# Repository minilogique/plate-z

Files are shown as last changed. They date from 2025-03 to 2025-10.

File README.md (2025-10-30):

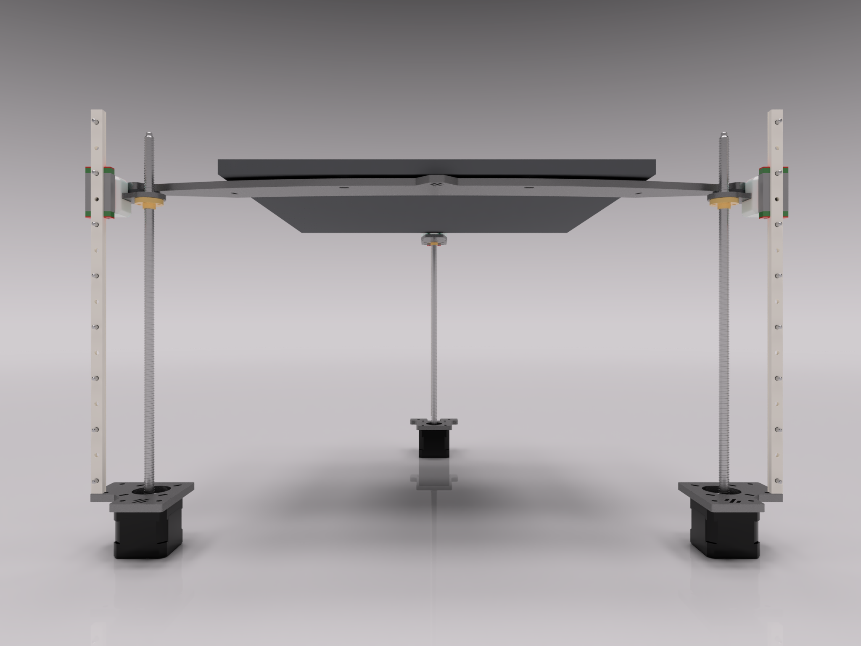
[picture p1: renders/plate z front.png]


A more industrial look and feel for the Voron Trident Z-assembly. Also greatly slims the whole Z-assembly and adds extra usable Z-height by making the bed itself as a part of the Z-kinematics. Keep in mind, that I do not own an official Voron but instead an adaption from Flying Bear Reborn 2 and this whole process is not complete and that the front carriers and carrier plates can be used to replace printed pieces as far as I'm concnerned, will check it once, again, I have gotten the CAD file of Trident. Flying Bear Reborn 2 owners are good to use these parts as in my printer it's been all happy for the last 200+ printing hours with more than 60C enclosure temperatures.

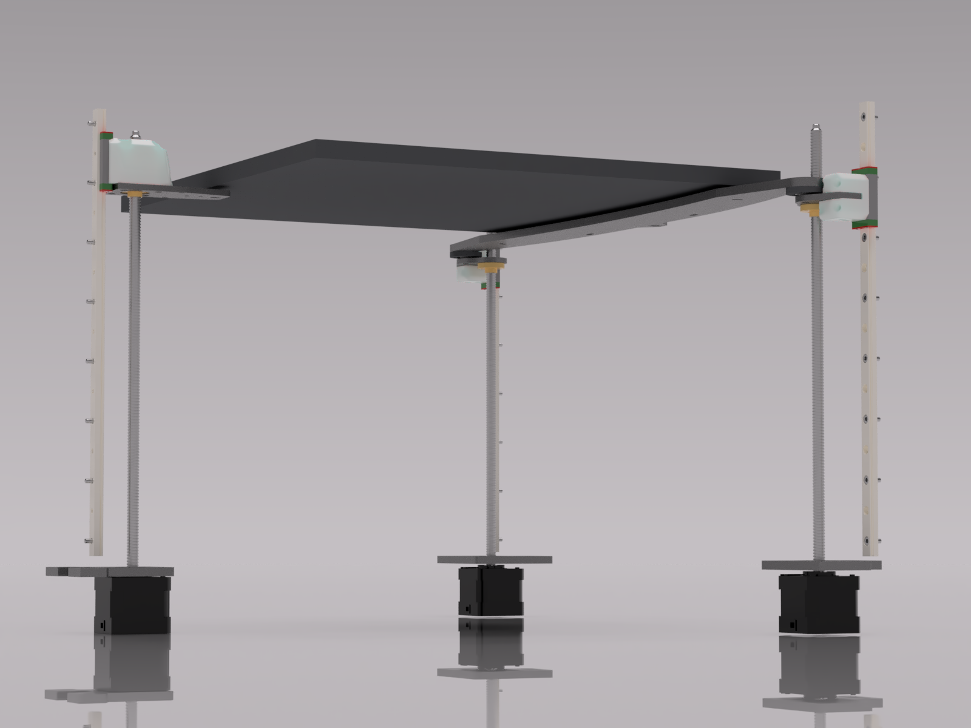
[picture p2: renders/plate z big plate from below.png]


The bigplate as I like to call it, is only piece connecting two points of the Z-gantry other than the bed itself. This is because of needed movements in case metal swells a bit bigger with heat and give way for the stress to go somewhere. I have yet to create the correct size bigplate for the bed because I created all this from a Trident 250 CAD and butchered it pretty badly. Flying Bear Reborn 2 owners are good to go as it's proven for hundres of hours and I have had no issues with it. Voron Trident bigplate DXFs will be created in near future after I have found the CAD files and correct measurements for Trident 250, 300 and 350.

I recommend to cut the front plates out of AT LEAST 4mm aluminium but go for 6mm, however I used 4mm stainless steel for fronts and 6mm for rear and everything is great. Seems that the rear stepper piece is happy with just two M4 bolts holding it in and it does not move nor bend under a bit more than normal printing conditions. Front plates have adjustabilty option to fine tune the stepper location as the bed will go really low compared to 2020 frame and otherwise very bulky assembly. The printable pieces that carry the plates are recommended to print from material that can resist at least 100C, be it ASA-CF or something better as the heat is conducted throughout the framing and noone wants plastic melt at wrong places.

The bigplate or big X-plate has to be cut from 6mm stainless steel. I might fear the aluminum might be a bit too bendy, but if your printer has 6mm bed it should be fine.

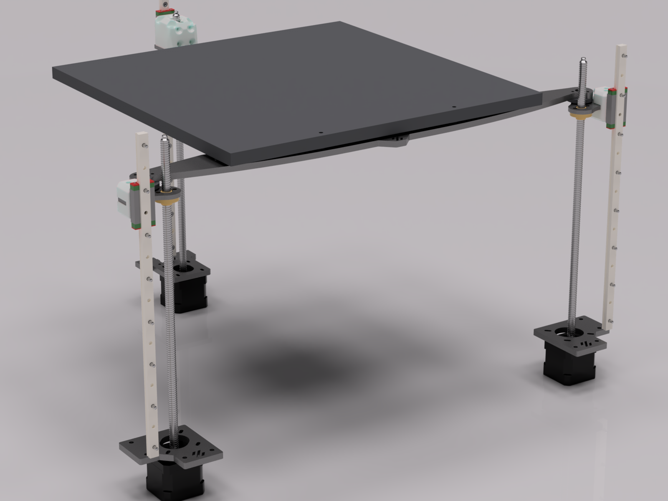
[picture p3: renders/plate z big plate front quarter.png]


To do this mod you might need to be able to quite possibly drill and tap your bed block for additional hardware.

Hardware I used with adapted Flying Bear Reborn 2 with Annex 350x350x12mm bed and 350mm version of FYSETCH 1000W heater:
- 8x M5x35 with nuts, washers are recommended; for attaching rear and front carriers to the plates. DO NOT overtighten the rear carrier as it might deform the part and misalign the rail cart bolt bores
- 4x M3x40 to attach rear plate carrier to the rear linear rail cart
- 10x M4x8 for 4mm stepper plates or 10x M4x10 for 6mm stepper plates
- 6x M3x12 with nuts for securing the spherical bearings from Voron BOM for front carriers, also these sandwich the bearings in place
- 6x M3x25 and 2x M3x20 for to attach printed front plate carriers to linear rail carts
- 2x M5x16 with nuts to tie X-plate and the spherical bearing together
- 6x M3x10 with nuts to attach brass Z-screws to front Z-assemblies or 6x M4x8 if you tap the threads into brass Z-screws and screw the bolts in them directly. Two bolts are enough, tighten them just enough that they are not loose and check after a while
- 2x M4x20 bolts if you dare to drill and tap two holes into the bed to secure the bigplate to it. Drill the holes in the middle of the ovals so it can still move, place an M5 nut for each of M4 bolts between the bigplate and bed to keep some space between the heater and bigplate so it is not siphoning too much heat from it
OR
2x M4x10 bolts if you just want to add two bolts in the plate as spacers to keep the heater away from the bigplate. I have it like this and the weight holds it steady.
- 2x M3x16 bolts close to the front corners of the bed. Again, holes have to be in the middle of the ovals to let the metals move. Most perfect solution would be with M3x20 bolts and with some really strong springs or couple of millimeters worth of springwashers.
- 12x M3x8, M3x10 or M3x12 bolts for steppers depending of what thickness you chose for the stepper plates - 4mm, 6mm or 8mm. You can add M3 slim washers to the top below the bolt heads. Screw them almost tight, back up half a turn, home the printer and then lower the bed as low as you can and adjust the steppers so the Z-screws are properly upright. Hold the Z-screws from the top and tighten one or two bolts per stepper and that is enough so you can raise the bed high enough for you to acces rest of the stepper bolts and tighten them properly
- 1x M3x16 bolt with a nut to the rear. Put the bolt in from the top of the bed, under the magnet line and tighten it. Once the bed is installed, add a spring or springwasher from below with another nut to secure it to the rear plate. Not the most elegant solution, but it's not designed be rigid and also not designed to be slanted more than few degrees. Bed will be held in position by front carriers and rear is just for support from a third point.

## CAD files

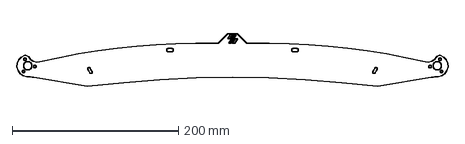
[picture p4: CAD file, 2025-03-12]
DXF/FBR2 bigplate X-plate.dxf
519.1 x 63.6 mm

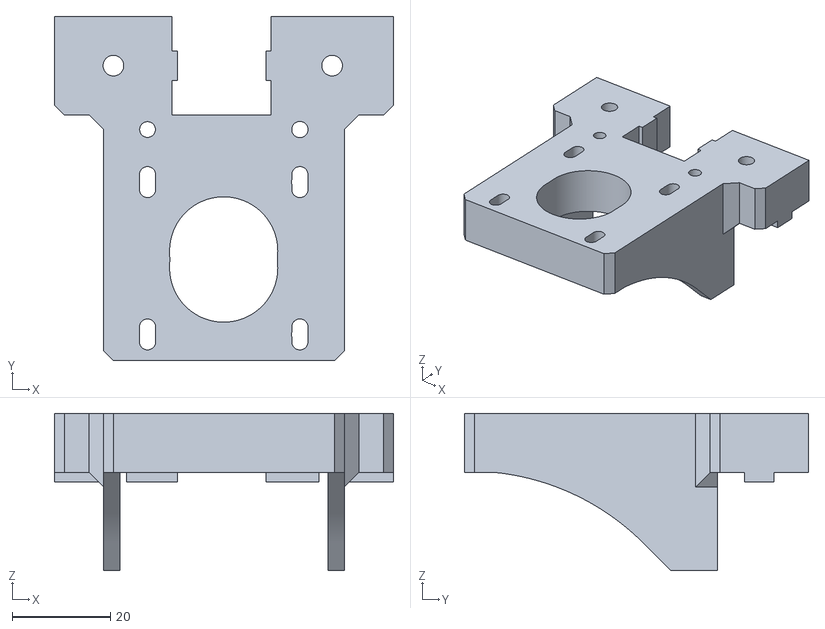
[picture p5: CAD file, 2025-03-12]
print files/plate-z printable rear stepper carrier.stl
69.0 x 70.0 x 32.0

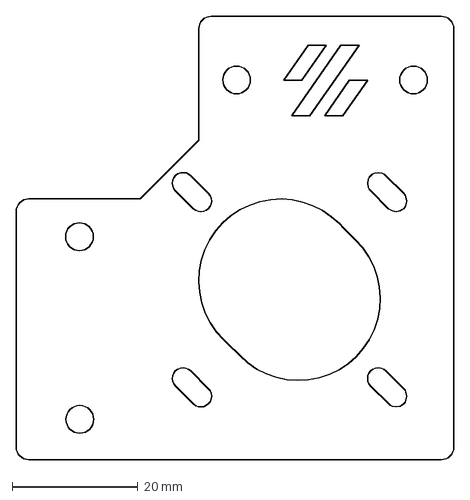
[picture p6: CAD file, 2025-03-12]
DXF/front right stepper plate.dxf
69.5 x 70.4 mm

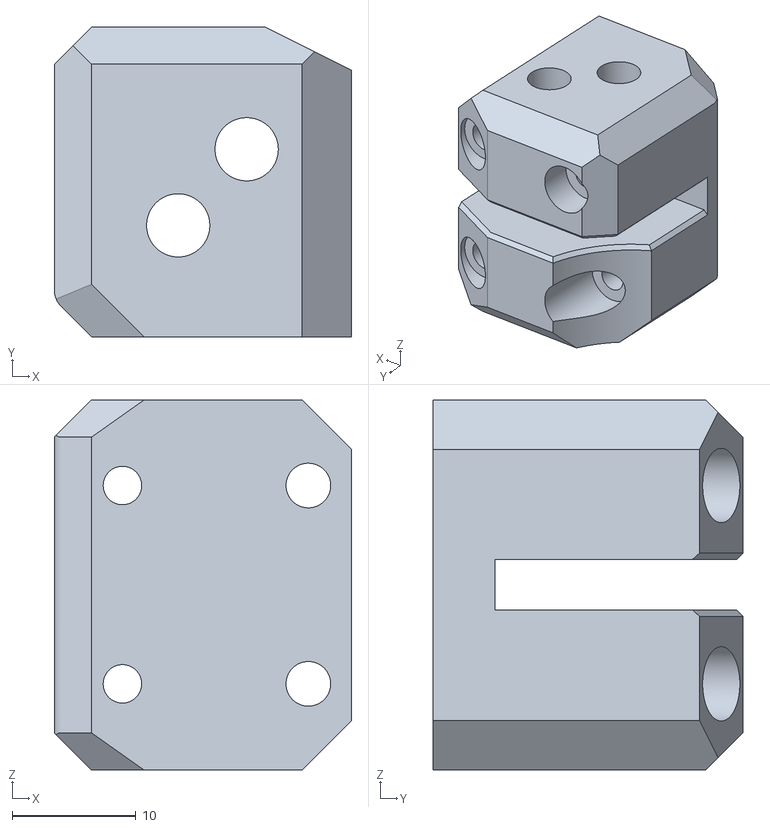
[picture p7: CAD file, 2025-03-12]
print files/plate-z left plate carrier for MGN9H.stl
24.0 x 25.0 x 29.9

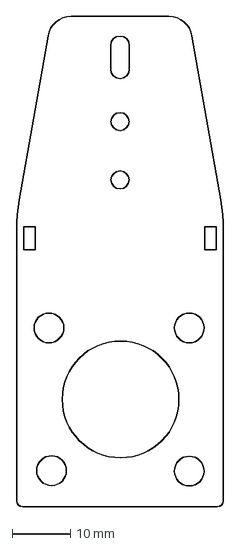
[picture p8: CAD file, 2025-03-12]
DXF/rear carrier plate.dxf
35.4 x 84.0 mm

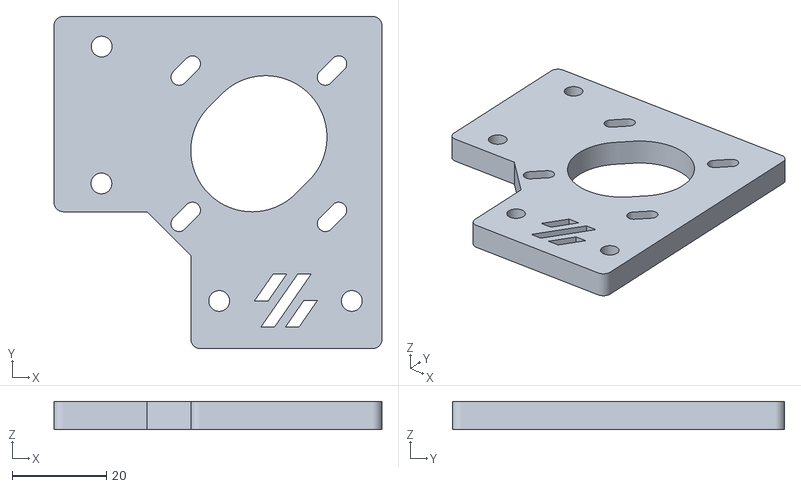
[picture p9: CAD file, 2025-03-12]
print files/plate-z printable left stepper mount.stl
69.5 x 70.4 x 6.00

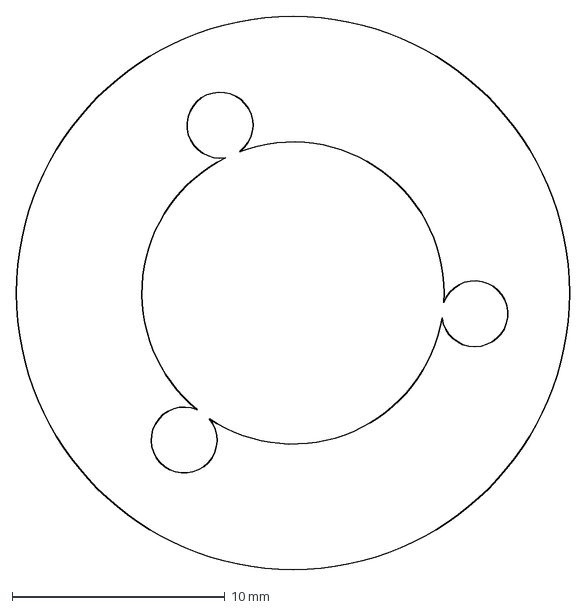
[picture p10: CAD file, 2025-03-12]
DXF/2x spherical bearing brace.dxf
26.0 x 26.0 mm

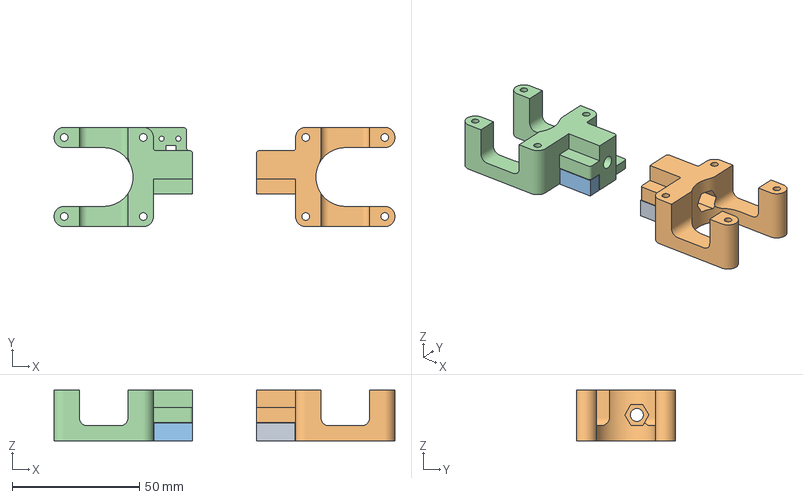
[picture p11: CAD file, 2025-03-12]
print files/AB stepper tensioners for aTSS plates with integrated endstop switch.3mf
133.8 x 39.0 x 20.0 mm

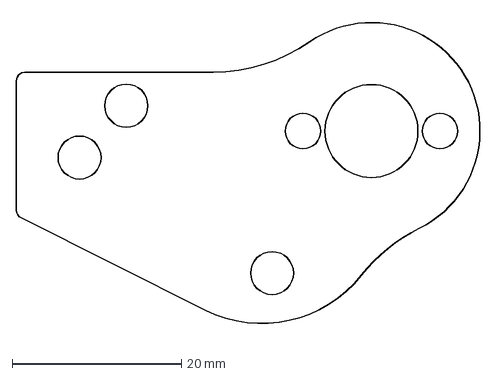
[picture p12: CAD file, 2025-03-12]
DXF/2x front carrier.dxf
54.9 x 37.9 mm

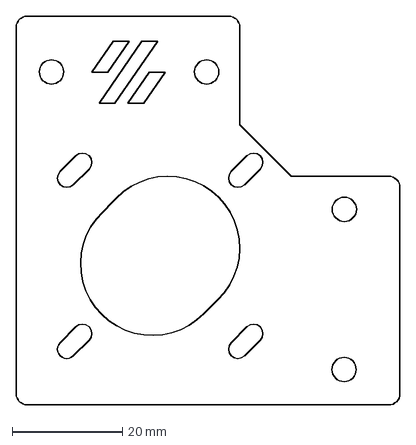
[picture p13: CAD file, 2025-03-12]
DXF/front left stepper plate.dxf
69.5 x 70.4 mm

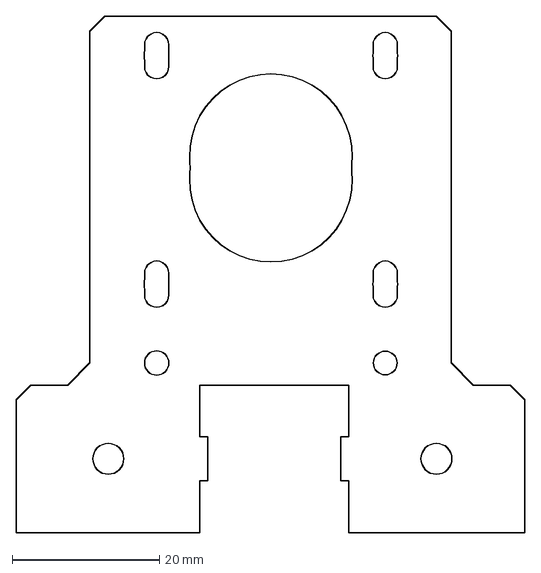
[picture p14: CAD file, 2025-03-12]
DXF/rear stepper plate.dxf
69.0 x 70.0 mm

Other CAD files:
print files/plate-z right plate carrier for MGN9H.stl
print files/plate-z printable right stepper mount.stl

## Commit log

2025-03-12 first upload
    [2x front carrier.dxf, 2x spherical bearing brace.dxf, AB stepper tensioners for aTSS plates with integrated endstop switch.3mf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]
2025-03-12 fixed renders
    [plate-z left plate carrier for MGN9H.stl, plate-z right plate carrier for MGN9H.stl]
2025-03-12 Create FBR2 bigplate X-plate.dxf
    [FBR2 bigplate X-plate.dxf]
